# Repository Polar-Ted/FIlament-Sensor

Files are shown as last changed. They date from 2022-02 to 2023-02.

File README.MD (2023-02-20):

[Original THingiverse post](https://www.thingiverse.com/thing:4781812)

The Cube is an optical filament motion sensor designed to use your old direct drive hobb gear extruder, The body mimics a Nema 17 stepper so almost any extruder kit can be used to guild the filament. The encoder has 36 slots and should provide down to 2mm jam or runout detection. I have tested it running at 5mm.
It will work with whatever size filament your extruder kit can handle and since it's driving an encoder wheel material transparency isn't an issue.

It uses a standard red board optical end stop with the socket on the opposite side from the sensor.

The concept was to build an motion sensor using standard 3D printer parts you may have as spares and common fasteners you can get at your local hardware store

The body has cavities for 8 M3 nuts that will be embedded in the print using the pause and insert function ( see your slicer documentation)

The back cover has a 31mm bolt circle so it should fit most Nema17 motor mounts
It's a simple block so it can easily be remixed into a custom mount of your design

Hardware needed.

A single hobb extruder kit        
m5 x40 hex bolt - pan , hex or socket head will work.      
M5 nut      
8 x M3 x 14mm screws      
8 M3 nuts      
2 x m3 x 6 screws      
2 x 625 bearings ( I scavenged some from old carriage wheels )      
Whatever M3 lengths your extruder needs      
1 optical end stop      

You need to have M600 Filament change enabled in Marlin and M412 enabled for runout detection with a runout distance set. If Marlin does not see a pulse from the sensor in the set filament runout distance it will trigger an M600 to unload and let you re feed the filament.

I'll work on adding notes to configure Filament change in Marlin.

In Reprap (Duet) I have it set for 0.6 pulses pr mm. I got the following results after monitoring it's output on a print.

M591 D0
Pulse-type filament monitor on pin servo0, disabled, sensitivity 0.977mm/pulse, allowed movement 60% to 160%, check every 3.0mm, measured sensitivity 0.982mm/pulse, measured minimum 97%, maximum 102% over 81.5mm

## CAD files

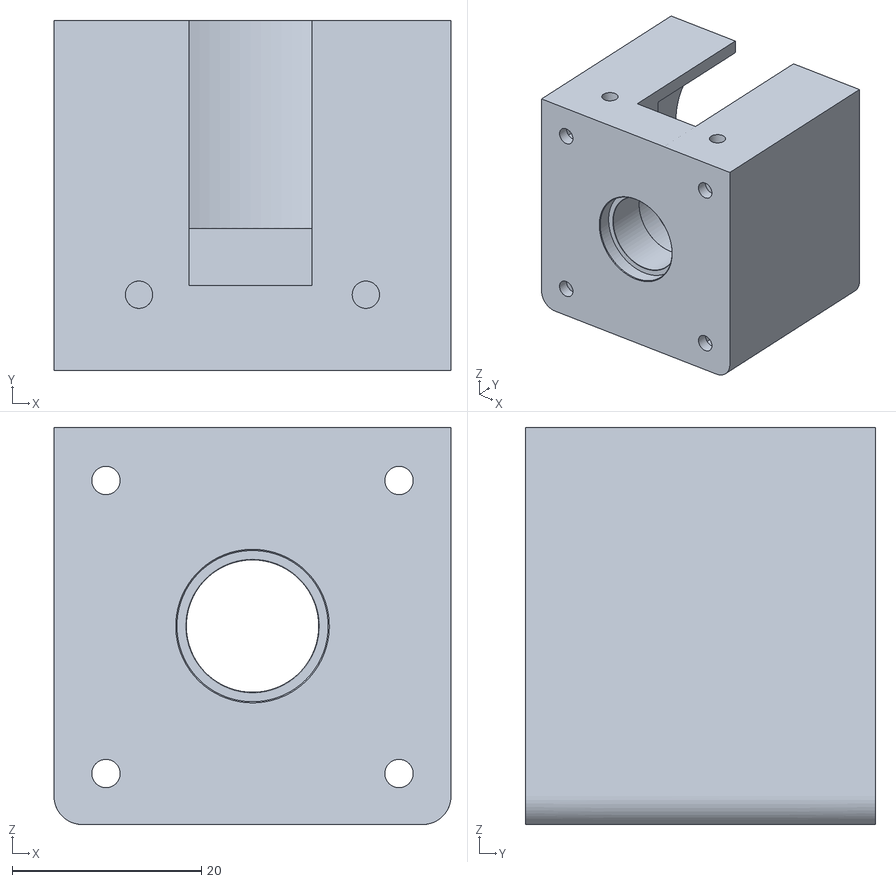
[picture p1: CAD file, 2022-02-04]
Main Body Filimant Monitor v15.stl
42.0 x 37.0 x 42.0

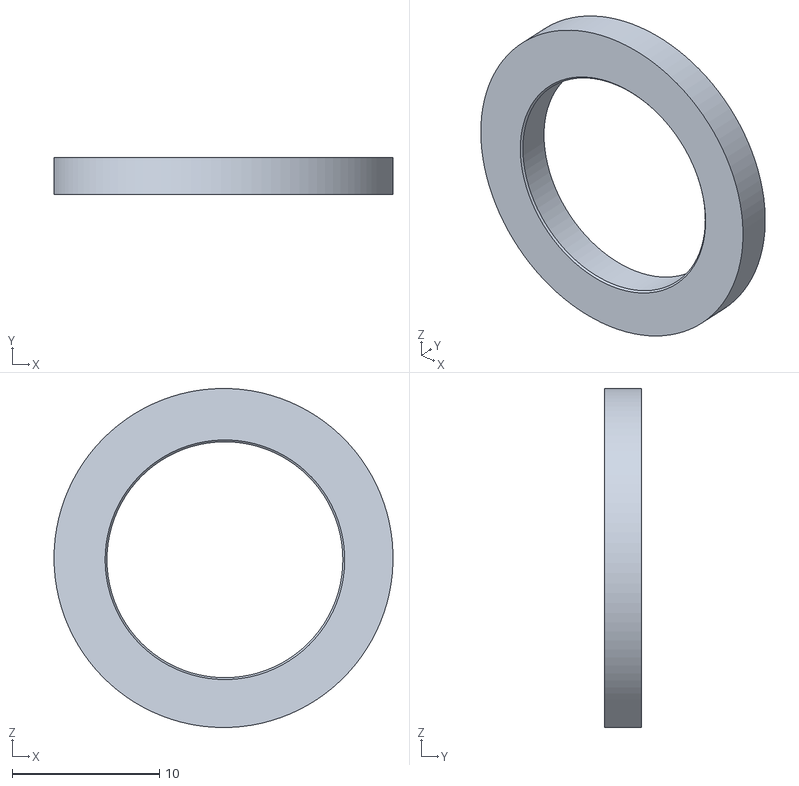
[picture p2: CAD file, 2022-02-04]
Snout ring Filimant Monitor v15.stl
23.0 x 2.50 x 23.0

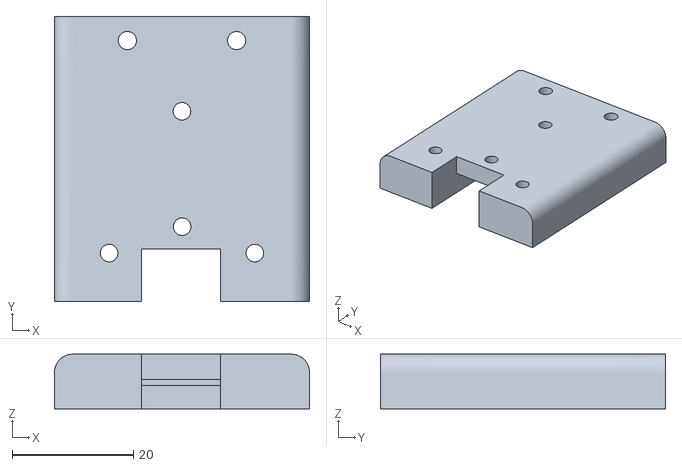
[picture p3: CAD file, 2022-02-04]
Sensor Mount Filimant Monitor v14.stl
42.0 x 47.0 x 9.00

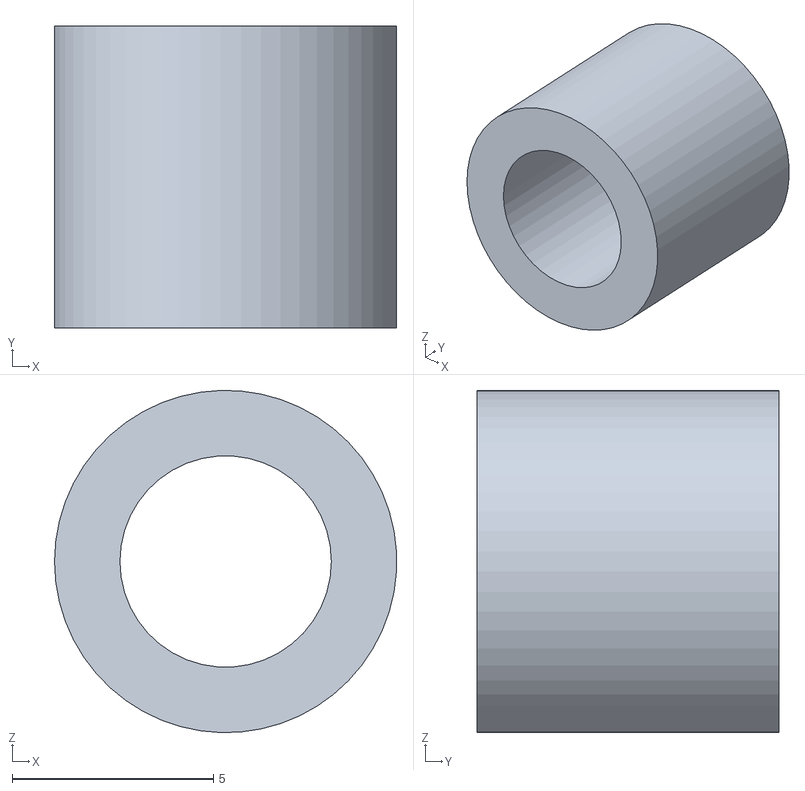
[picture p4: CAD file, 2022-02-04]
Axle spacer filimant Monitor v8.stl
8.49 x 7.50 x 8.50

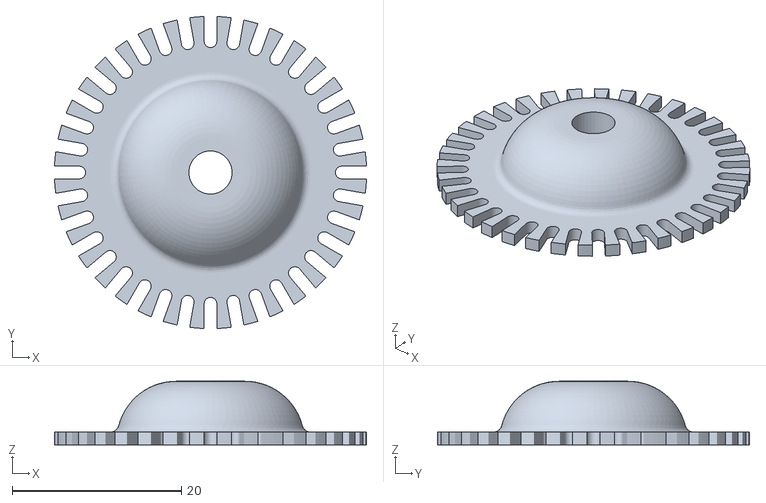
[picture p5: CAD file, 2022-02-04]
Encoder Wheel R19.stl
36.8 x 36.8 x 7.50

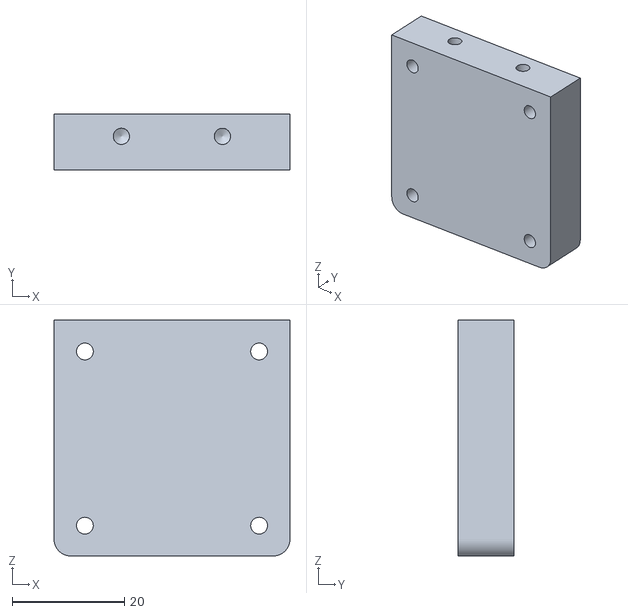
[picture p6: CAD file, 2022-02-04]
Back Plate Filimant Monitor v8.stl
42.0 x 10.0 x 42.0
